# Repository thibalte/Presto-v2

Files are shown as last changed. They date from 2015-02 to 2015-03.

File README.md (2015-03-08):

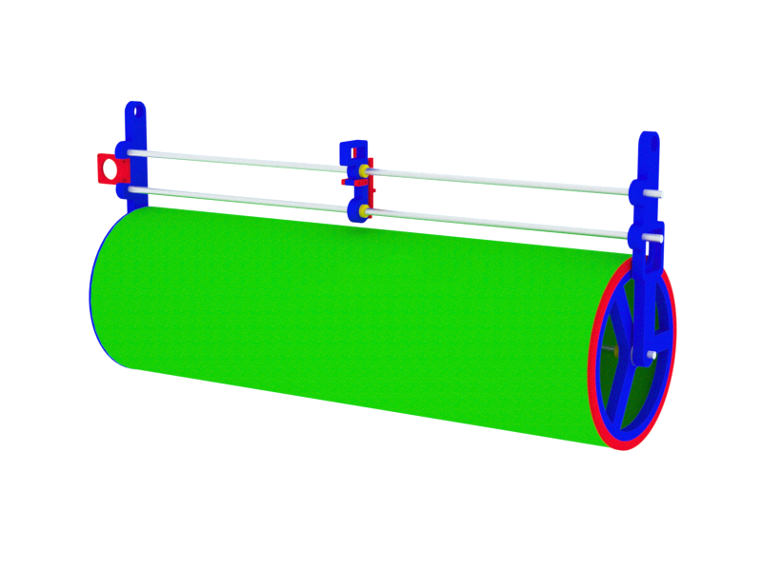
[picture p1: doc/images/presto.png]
assembly


# Presto v2

*The project is currently in development, this repo is not complete yet.*

Presto is an open-source vector plotter designed to handle 70*100cm stock paper. It features a universal gripper to accomodate any tools from super-thin pencils to large paintbrushes.

Updates in v2:

- upgraded hardware for easy and fast (dis)assembly
- easy electronics, no need for 2 arduinos, servo is driven via a small ATTiny chip as slave
- host software for auto/manual printing, on-the-fly G-Code generation
- smaller part count, better integration of components: faster build, simpler manufacturing

## TODO

- design arduino shield PCB including 2 stepper drivers, 1 ATTiny45 to avoid the cable salad and don't have a slave board
- test clip-in system for shafts in side frames instead of current pressure screws, test plywood flex

## Get Started

go to the [How-To](howto.md).

## References

- [dented gear generation](http://hessmer.org/gears/InvoluteSpurGearBuilder.html).

## Thanks

Improvements on side frames and x-carriage thanks to Matt Maurer, Fabian Ritzi, Kevin Rentz @ Hyperwerk, Basel CH.

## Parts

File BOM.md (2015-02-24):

# Hardware

from [IGUS](http://www.igus.ch)
- 3 AWMP-12, 1087mm, smooth aluminum precision shafts
- 4 RJMP-12, plastic bushings
- 1 NS-01-17, 100mm, linear guiding rail, aluminum
- 2 NW-02-17, P, pre-constrained plastic linear sliders

from [MAEDLER](http://www.maedler.ch)
- 1 26302000, dented wheel, bronze
- 1 16022600, dented pulley, aluminum
- 2.5m 16060000, T2.5 6mm width, dented belt

from [SPARKFUN](https://www.sparkfun.com)
- 2 Nema23 stepper motors, ROB-10847
- 1 Servo, Hitec HS-422 (Standard Size), ROB-11884
- 2 EasyDriver, ROB-13226
- 1 Arduino Uno, DEV-11021
- 1 ATTiny85, COM-09378
- 1 USB cable A to B, generic

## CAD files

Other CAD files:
drawings/assembly.3dm

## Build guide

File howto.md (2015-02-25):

## Get started with Presto

*This is a temporary guide, will be edited further*

- download the repo
- order the parts in the BOM
- machine the parts in the build folder
- assemble the parts together
- assemble electronics, stepper motors and servo
- flash the firmware to the ATTiny
- flash GRBL to the Arduino Uno (with HexUploader for example on OSX)
- configure GRBL with the settings in grbl-settings.txt
- start the client software
- import your SVG
- print!

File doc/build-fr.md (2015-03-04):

# PRESTO - Guide utilisateur v0.1 FR

0. Outils
1. Terminologie
2. Assemblage mécanique
3. Branchements électriques
4. Logiciel

## 1. Outils

- 1 tournevis plat
- 1 tournevis cruciforme
- 1 clé Allen 5
- 1 pince plate
- 1 marteau

## 2. Terminologie

### X-axis-side


### Y-axis-side


### Y-axis-frame


### Charriot


### Clip pour courroie


## 3. Assemblage mécanique

- Insérer 3 vis M5 20mm dans les 3 trous du **Y-axis-side** et **X-axis-side**, ne pas les visser trop, elles ne doivent pas sortir à l'intérieur du trou de passage des axes

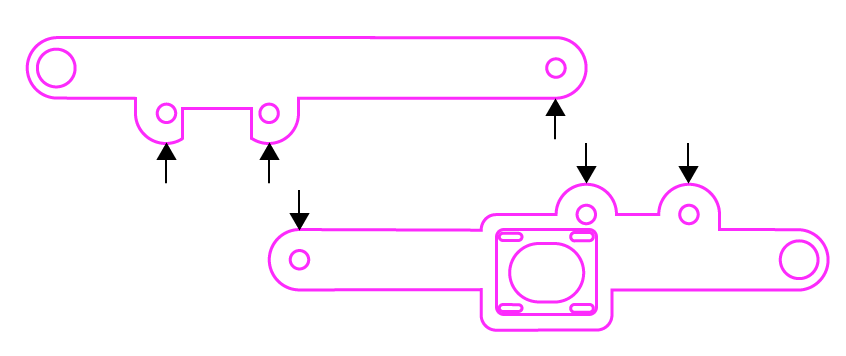
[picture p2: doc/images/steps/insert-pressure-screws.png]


- Insérer les 3 axes dans les 3 trous du **Y-axis-side**. les axes ne doivent pas dépasser, ils doivent apparaître à fleur de l'axe. les axes doivent dépasser du côté opposé à la croix noire.

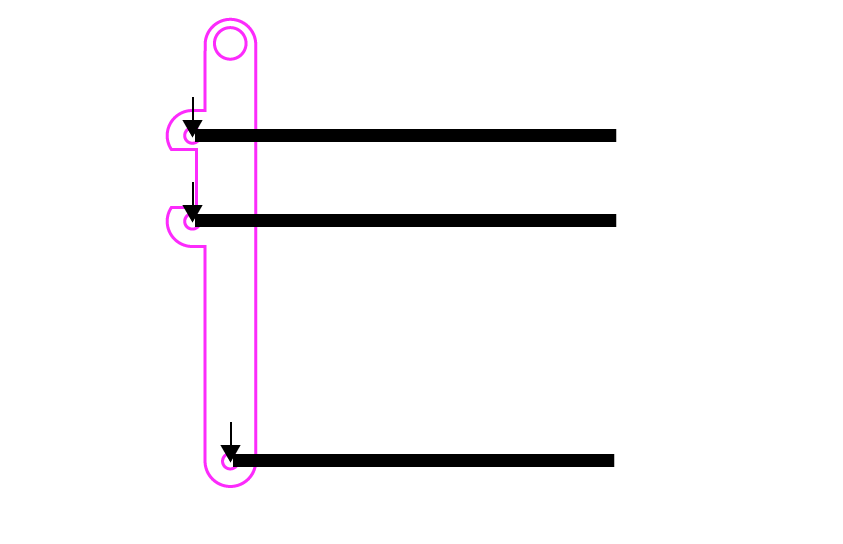
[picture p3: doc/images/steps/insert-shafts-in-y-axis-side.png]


- Vérouiller les 3 axes avec les 3 vis de pression du **Y-axis side**. Pas besoin de serrer fort, une fois atteint l'axe, 1/8 de tour suffit à bloquer l'axe pour l'empêcher de se déplacer.

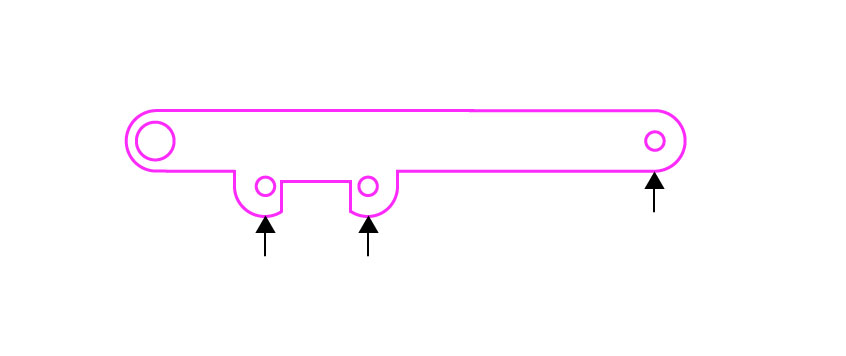
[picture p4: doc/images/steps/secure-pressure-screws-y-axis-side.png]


- Insérer le tube et ses 2 rondelles métalliques de chaque côté, le **charriot** sur les 3 axes suivant ce modèle:

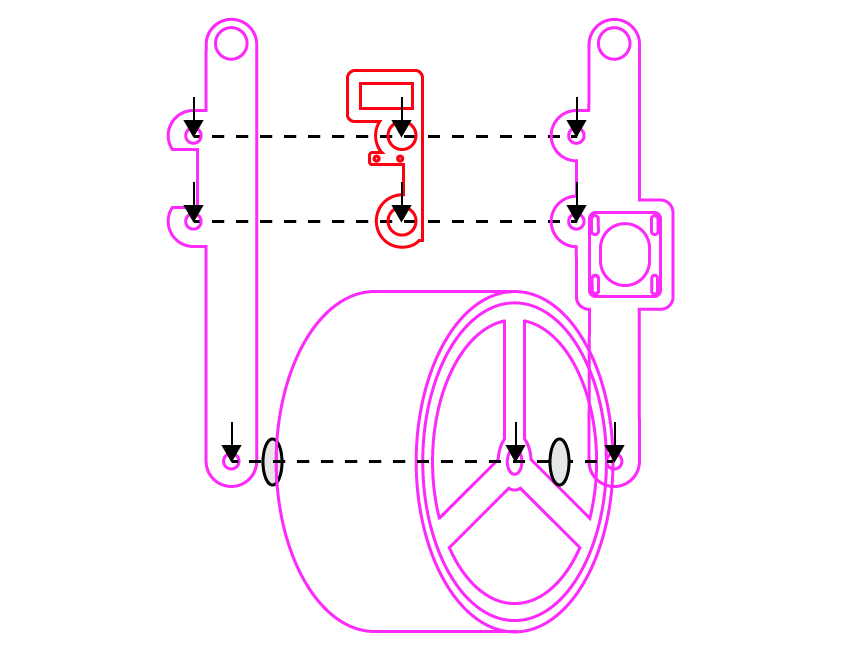
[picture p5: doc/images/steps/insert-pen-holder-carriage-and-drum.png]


- Pour insérer le **X-axis side**, il est recommandé de placer l'assemblage debout sur le **Y-axis-side**, il suffit de taper gentiment avec un petit marteau sur le long du **X-axis-side** pour qu'il s'enfile sur les 3 axes (à noter, les axes sont plus long d'environ 1-2cm, c'est normal qu'ils dépassent de ce côté):

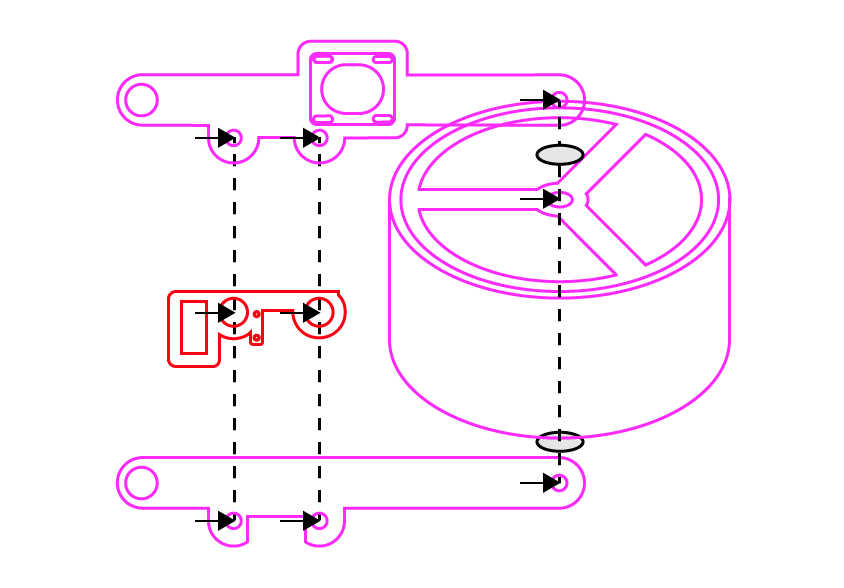
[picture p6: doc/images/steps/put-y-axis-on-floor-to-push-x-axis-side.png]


- Lorsqu'il n'y a plus de jeu entre les 2 **X-axis-side** et **Y-axis-side**, les rondelles, et le tube (mais que le tube puisse tourner librement sur son axe), on peut vérouiller la position avec les 3 vis de pression du côté **X-axis-side**.

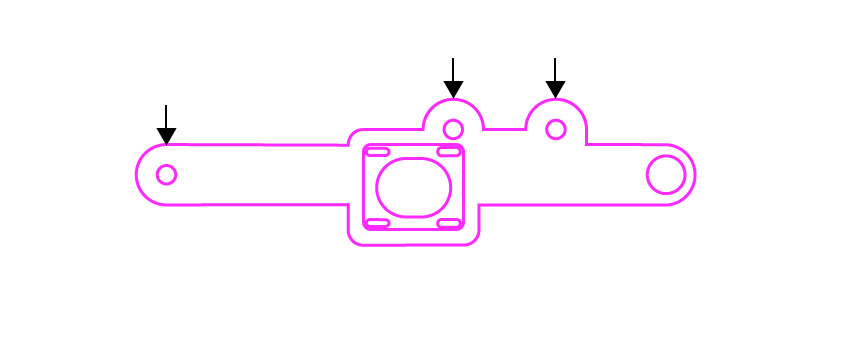
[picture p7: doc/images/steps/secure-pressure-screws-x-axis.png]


- On peut à présent accrocher l'assemblage aux cordes. En premier, passer les 2 mousquetons et boucles dans les trous en haut des **X-axis-side** et **Y-axis-side**, accrocher la corde quelque part, puis suspendre l'assemblage, à environ 1m du sol, donne un bon confort de travail.

- Installer le **Y-axis-frame** sur le **Y-axis-side**, le visser par les 2 vis M5 30mm. /!\ ATTENTION /!\ ne pas serrer trop fort les vis sur le plexiglass, il risque de craquer si trop fort. Si la pièce ne bouge plus et qu'il n'y a pas de jeu cela suffit.

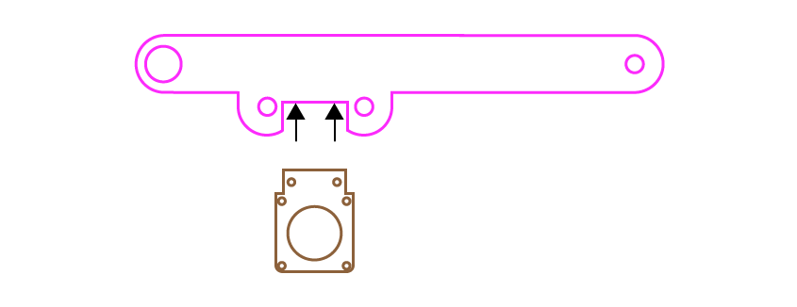
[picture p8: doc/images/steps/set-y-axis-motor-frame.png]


- Installer le **Y-axis-pulley** (la vis M5 40mm avec 2 rondelles et un roulement à bille dans le sachet) sur le **X-axis-side**, ne pas visser en entier, laisser environ 1cm de séparation entre le bois et le boulon collé sur la vis (il faut utiliser soit une clé hexagonale, soit utiliser une pince plate et pincer la tête hexagonale pour visser):

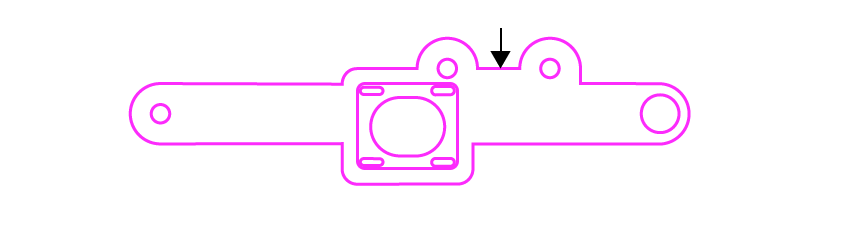
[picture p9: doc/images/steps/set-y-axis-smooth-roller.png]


- Installer le **Y-axis-motor**, le moteur avec une roue dentée de couleur argent, sur le **Y-axis-frame** (le moteur doit être du côté **Y-axis-side** du plexiglass, côté bois) (si les vis tournent dans le vide, c'est parce qu'il faut bien bloquer les boulons qui tournent dans le vide, on peut insérer le tournevis plat pour boquer les boulons pendant que l'on visse):

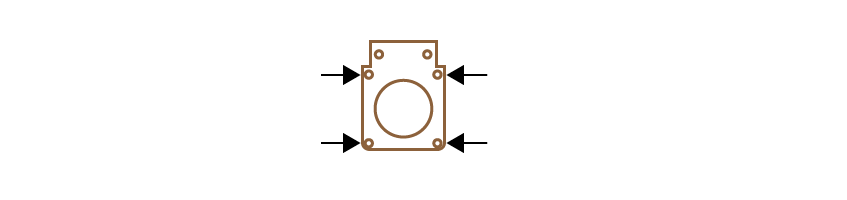
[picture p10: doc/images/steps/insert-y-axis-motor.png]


- Insérer les 2 **belt-clips** de chaques côté du **charriot**, avec les 2 vis pointant du côté **Y-axis-side**:

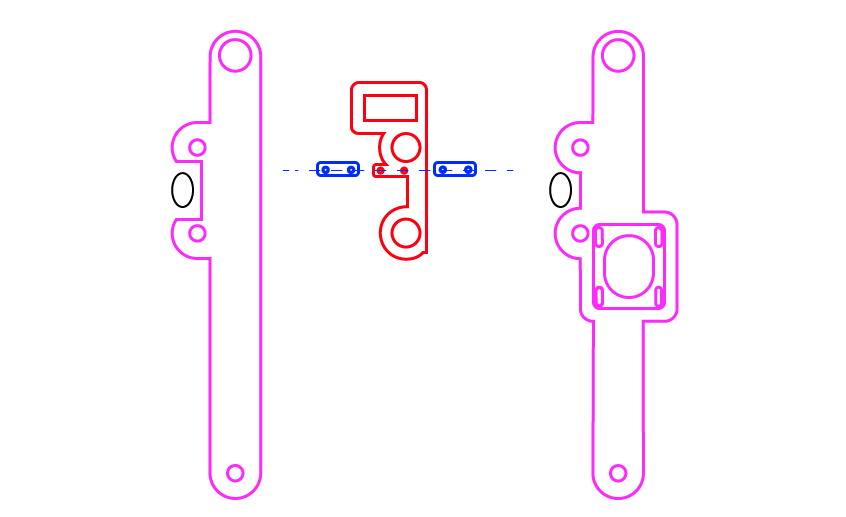
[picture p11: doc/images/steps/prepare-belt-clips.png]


- Vérifier que le charriot coulisse bien sans frottement majeur, il faut uniquement le pousser par la partie ou se situe les 2 flèches noires, autrement on le pousse de travers et c'est normal qu'il se bloque (en gros: il faut le pousser au niveau du milieu entre les 2 axes, si on le pousse par le haut il y'a du porte-à-faux et ça coince). Si il y'a un frottement anormal, déserrer les vis de pression d'un côté et essayer de réaligner les 2 **X-axis-side** et **Y-axis-side**: un frottement excessif apparait si les 2 côtés ne sont pas bien parallèles, du coup les 2 axes ne sont pas parallèles non plus et le charriot coince.

- Insérer la courroie dentée en passant autour du **Y-axis-motor** et de la poulie du côté **X-axis-side**, et pincer la courroie en la passant sous les 2 **belt-clips**. /!\ ATTENTION /!\ ne pas visser d'un coup une des 2 vis, visser petit à petit les 2 côtés pour ne pas risquer de craquer la pièce. lorsque la courroie est presque pincée, la tendre pour qu'elle ne "flotte" plus.

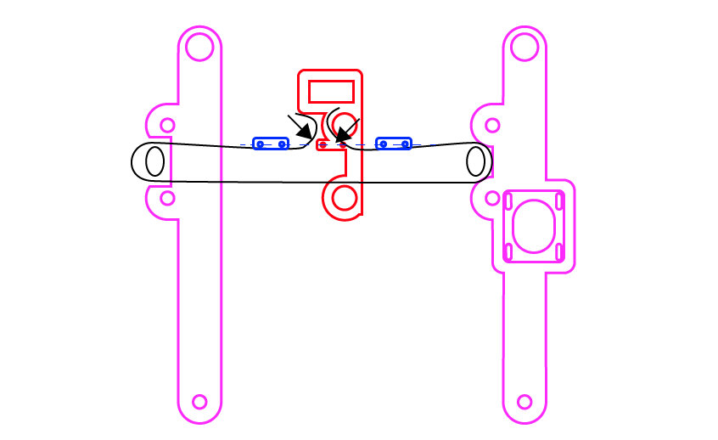
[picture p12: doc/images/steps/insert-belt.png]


- Insérer le **X-motor**, celui avec une roue dentée couleur laiton, dans son logement sur le **X-axis-side**. 2 vis M5 de 20mm sur les 2 trous du haut suffisent. /!\ ATTENTION /!\, pour l'instant ne pas serrer les vis à fond, laisser un peu de jeu pour que le moteur puisse être ajusté en hauteur. Faire faire des tours au tube pour voir si le moteur est positionné trop bas: le tube ne doit pas bloquer en faisant un tour entier et l'on ne doit pas sentir de force excessive. Vérouiller les 2 vis du moteur, vérifier à nouveau que le tube puisse correctement tourner sans rencontrer d'effort majeur, si oui, déserrer et réajuster la hauteur du moteur. Il ne sert à rien de serrer trop fort, si le moteur ne bouge plus, cela suffit afin de ne pas écraser le bois.

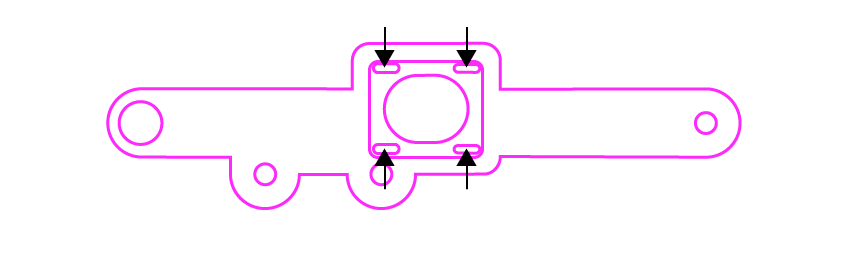
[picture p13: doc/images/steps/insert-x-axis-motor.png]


- Insérer le **pen-holder** (pièce assemblée en plexiglass) dans le **charriot**. Les 2 pièces en plastique jaune s'insèrent dans la glissière en métal du **charriot**. La partie en plastique blanche s'insére en enlevant la vis noire du servo-moteur du **charriot** et en y plaçant la partie en plastique blanche. /!\ ATTENTION /!\ ne pas enlever la partie en plastique blanche déjà présente sur le servo-moteur, sinon on perd la position du servo-moteur et c'est très embêtant à retrouver.

- La partie en plastique blanche, le bras du servo-moteur, doit être inséré avec le fil de fer en métal plié, déjà inséré dans le plexiglass en même temps, qui lie le bras du servo-moteur et la partie en plexiglass, c'est cette partie qui fait monter/descendre l'outil installé sur le **charriot**.

- Placer manuellement le **charriot** à environ 1cm du **Y-axis-side** en position de départ.

- L'assemblage mécanique est terminé!

## 4. Branchements électriques

- Sortir l'assemblage électronique ainsi que la carte Arduino.

- Brancher les fils seuls correspondants sur la carte Arduino: GND, 13, ainsi que la rangée 2-6 correspondante sur les chiffres indiqués sur les sorties de l'Arduino.

- Brancher les câbles des moteurs suivant les codes couleurs des petites cartes rouges

- Brancher le câble de servo moteur sur le câbe à 3 brins, en suivant ce sens: Noir dans Noir

- Ne pas toucher le potentiomètre réglable: il sert à ajuster la hauteur à laquelle l'outil se lève lorsque l'on imprime. Uniquement à utiliser pour personne expérimentée.

- Brancher le câble USB à l'Arduino et l'ordinateur

- Visser le câble de prise électrique murale dans le bloc d'alimentation (bloc en métal avec des trous) suivant les étiquettes

- Visser le câble d'alimentation noire suivant les étiquettes au bloc d'alimentation

- Brancher la prise noire ronde mâle venant du bloc d'alimentation dans la prise femelle de l'assemblage électronique: une petite lumière sur les cartes rouges doit s'allumer

- /!\ NE JAMAIS BRANCHER OU DéBRANCHER LES CABLES DES MOTEURS LORSQUE L'ENSEMBLE EST BRANCHé AU BLOC D'ALIMENTATION SOUS PEINE DE GRILLER LES PETITES CARTES ROUGES (LES DRIVERS DES MOTEURS PAS-à-PAS)

- Les branchements électriques sont terminée!

## 5. Logiciel

- Télécharger et installer Processing (http://www.processing.org), Arduino (http://www.arduino.cc), ainsi que la libraire pour Processing: Geomerative (http://www.ricardmarxer.com/geomerative/), et ControlP5 (http://www.sojamo.de/libraries/controlP5/) (les télécharger et les placer dans le dossier ~/Documents/Processing/librairies, par exemple, peut varier suivant l'installation) Installer les drivers FTDI pour la communication avec l'Arduino (http://arduino.cc/en/Guide/Howto)

- Ouvrir le programme Mission Control dans le dossier Github avec Processing: simplement ouvrir missionControl.pde avec Processing.

- Trouver le nom de port sur lequel est branché l'Arduino (en regardant la liste des ports avec le logiciel Arduino) et remplacer celui présent dans le logiciel Mission Control, c'est la variable String appelée **grbl** tout en bas de l'onglet "vars"

- Lancer le logiciel (cliquer sur la flèche Play en haut à gauche de l'écran)

- On peut à présent importer un fichier SVG de taille 700x1000mm, et cliquer sur Print pour faire une impression. Pour l'instant ne pas mettre d'outil pour vérifier que les moteurs se déplacent correctement, si tout se passe bien, on peut fixer un stylo à environ 5-10mm de haut avec la pince incluse sur la partie en plexiglasse, en câlant le stylo dans les 3 parties en V.

- On peut manuellemnt sélectionner un tracé avec les boutons NEXT ou PREVIOUS et uniquement imprimer ceux-ci avec PRINT SELECTED. On peut revenir au point de départ avec HOME.

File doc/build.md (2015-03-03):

# unpack

# preparing the side supports

# push shafts into Y-axis side

# secure shafts

# slide drum and pen-carriage onto shafts

# push X-axis side onto shafts

# secure shafts on X-axis side

# suspend the assembled frame

# install Y-axis motor and pulley

# install belt clips on pen carriage

# install belt and secure it

# install X-axis motor and secure with right tension

# install pen holder

# attach pen holder to servo

# connect motors and servo to electronic

# connect power supply

# connect usb to computer

# install Processing, ControlP5 and Geomerative libraries

# find Arduino port name

# set port name in Mission Control

# start Mission Control

# Print!

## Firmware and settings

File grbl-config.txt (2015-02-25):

$0=25.464 (x, step/mm)
$1=24.615 (y, step/mm)
$4=15000.000 (default feed, mm/min)
$5=15000.000 (default seek, mm/min)
$8=100.000 (acceleration, mm/sec^2)

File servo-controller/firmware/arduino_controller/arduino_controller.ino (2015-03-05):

//
// SERVO CONTROL with arduino
// 
// connect GND from arduino to other Arduino
// connect pin 13 to pin 13 of other Arduino
//
// connect GND of Arduino to BLACK cable of servo
// connect 5V of Arduino to RED cable of servo (middle cable)
// connect pin 9 of Arduino to ORANGE cable of servo (opposite of black/brown)
//

#include <Servo.h> 

int in = 13;

Servo servo;

// valeurs de position haute et basse à régler en testant M3 et M4 depuis le moniteur série d'Arduino (de 0 à 180 degres)
int up = 30;
int down = 150;

void setup() {
  servo.attach(9);
  pinMode(in, INPUT);
}

void loop() {
  if (digitalRead(in)){
    servo.write(down);
  } else {
    servo.write(up);
  }
  delay(10);
}

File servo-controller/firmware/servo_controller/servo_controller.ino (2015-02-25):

//
// Presto v2 Servo Controller firmware
// Thibault Brevet, 2015.
//
// flash on ATTiny45/85
//

#include <SoftwareServo.h>

// settings
SoftwareServo servo;
int in = 0;
int pot = A1;
int up = 0; // servo doesnt like super small value

void setup()
{
  // init stuff
  pinMode(in, INPUT);
  pinMode(pot, INPUT);
  servo.attach(1);
  // overwrite defaults
  servo.setMinimumPulse(500);
  servo.setMaximumPulse(2400);
}

void loop() {
  // check what setting is with the pot
  int down = map(analogRead(pot), 0, 1024, 0, 180);
  int val = digitalRead(in);
  delay(1);

  // if the input is HIGH set the servo down
  if (val){
    // move down
    servo.write(down);
  } else {
    // else move up
    servo.write(up);
  }

  SoftwareServo::refresh();
  delay(10);
}

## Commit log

2015-02-20 added bom
2015-02-20 edited BOM
2015-02-24 added new global assembly, edited readme, bom
2015-02-24 added servo controller code and schematics
    [servo-controller.sch]
2015-02-24 moved folder structure
    [servo-controller.sch]
2015-02-24 added description to servo controller firmware
2015-02-25 added GRBL config and edited servo controller firmware
    [grbl-config.txt]
2015-02-25 started working on the design of the arduino shield pcb
    [shield.brd, shield.sch]
2015-02-25 worked on the schematics of the shield, corrected a4988 wiring
    [shield.sch]
2015-03-01 added Mission Control printing client, temporary screws list
2015-03-04 added ftdi driver install in doc fr
2015-03-05 added arduino controller
2015-03-08 added assembly image
    [assembly.3dm, assembly.dwg]
2015-03-08 cleanup and updated image with pen carriage ion wrong side
    [assembly.3dm, assembly.dwg]
